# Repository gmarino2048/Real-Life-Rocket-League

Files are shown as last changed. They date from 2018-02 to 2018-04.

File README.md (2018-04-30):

# SocCar: Arcade Style Car-Soccer Game

## Getting Started:

### Basic Instructions

1. Locate a set of Cars, Arena, and ball near you.

2. Make sure both Cars, and the Arena are powered on. The power switch is located on the bottom of each car. If the arena appears to be without power, ensure that it is plugged in.

3. Go to SocCar website

4. Click on Play Game

5. Create a New User

6. Sign in with User Information

7. Make sure that your car is on

8. Press Play Game

## Troubleshooting:

### Connectivity:
If a car appears to be having an issue receiving commands:
1. Check the LED located on the Arduino Board on each Car. If the LED is lit, the car is properly powered.
2. If the car was not properly powered, try to turn the car off and on again. If the car still appears to be without power, contact your nearest SocCar vendor.
3. If the cars are properly powered, turn them off and on using the power switch located on the bottom of the car. This will reset the connection.

### Driving Issues:

#### If the speed of a car seems to be inconsistent:
1. Check the Drive Gears on either side of the car. Make sure that both gears are standing straight. If they are not straight, apply light pressure until you have righted them. Restart the car and try it again.
2. If the drive gears are straight, check to see if the steering assembly is flexing so the front two wheels are angled. If this is the case, your steering assembly likely

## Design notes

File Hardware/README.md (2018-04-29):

# SocCar Project

## Hardware

There are two important components of the hardware for this project: the arena and the car. The arena will display the players' usernames and scores, and will relay that information back to the server. The car will listen for input from the server, and will move accordingly so that the player is able to control the car to get the ball into the goal.

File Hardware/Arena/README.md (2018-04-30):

# SocCar Project

## Arena

### API Connection

The API Connection folder contains all of the source code for the connection between the backend and the Arena. If you're interested, there are some functional unit tests in there under the [src](https://github.com/gmarino2048/Real-Life-Rocket-League/tree/master/Hardware/Arena/API%20Connection/API%20Connection/src) folder.

If you are unsure of the login credentials for the project, please see the `ID and Secret.txt` file included.

### Arena Hardware

#### Microcontroller Programming

To program each of the microcontrollers, navigate to the Arduino folder. There should be three microcontrollers total: an Arduino Due, a Particle Photon, and an Arduino nano. The following list gives the steps to program each microcontroller successfully.

- Arduino Due -- has the most pins, ARM Processor, is the largest device of the three
  - Using the arduino application, load the Arena-Controller.ino sketch onto this device
  - Reset the Controller

- Particle Photon -- has the least pins, is the smallest device, has a blinking RGB LED
  - Go to build.particle.io
  - Log in and register the device to your account (follow the prompted steps)
  - Copy and paste the Web-Connection.ino file into the code window
  - Click "Flash", and wait for the device to update

- Arduino Nano -- small, but has more pins than the Photon, has  green and yellow LEDs which blink occasionally
  - Using the arduino application, load the LCD-Controller.ino sketch onto the device.
  - Occasionally, the bootloader of the device will be erased to fit the entire volume of the sketch into memory. If this occurs and you cannot load the code, see [this example.](https://www.arduino.cc/en/Tutorial/ArduinoISP)
  - Once the code has been uploaded, see the guide below for connecting each of the components.

#### Microcontroller Connection

Using the above information, connect each individual component according to the diagram found below:

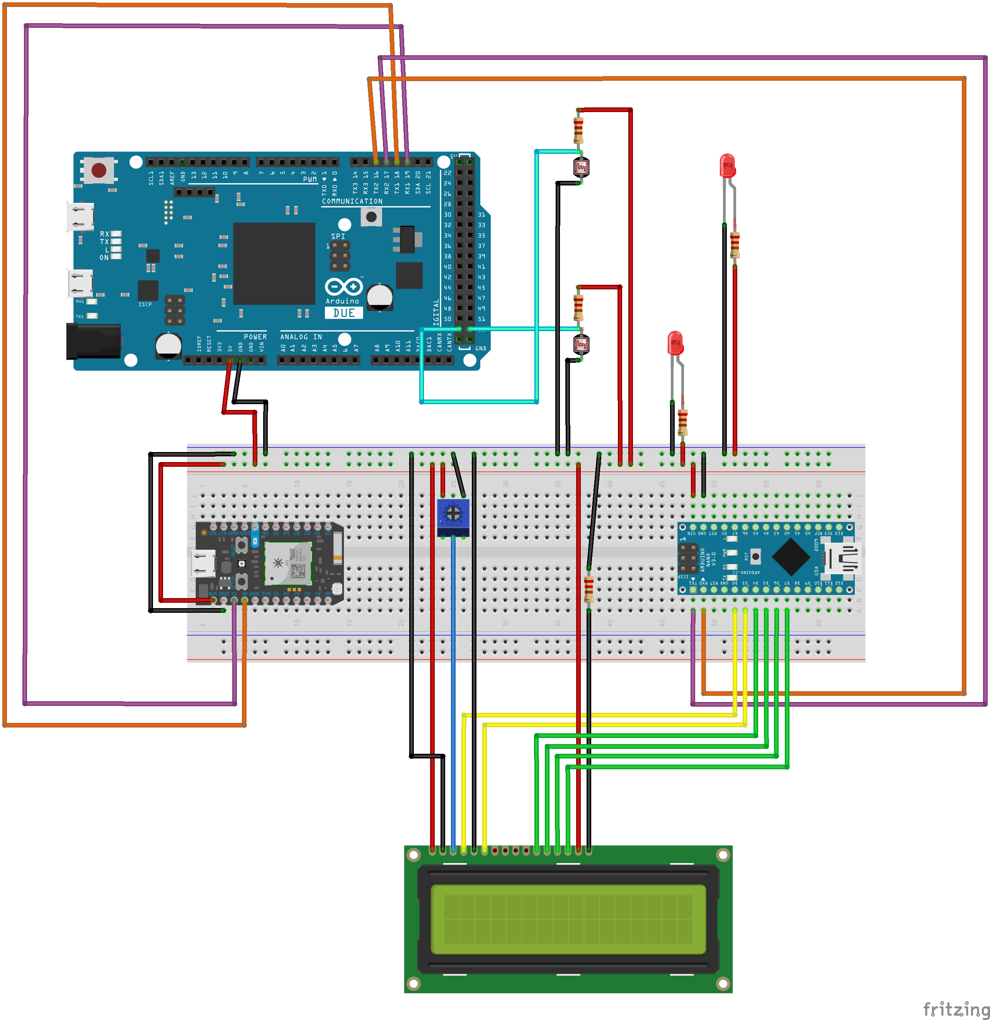
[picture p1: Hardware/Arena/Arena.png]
Arena Wiring Diagram


Note that the LCD Display is connected to the Arduino Nano, and the break beam sensors (modeled by a resistor and photoresistor in this case) are connected to the DUE.

Ensure that ALL of the connections are correct before supplying power to the devices, as incorrect connections could potentially damage certain components.

If you have any problems connecting the components, feel free to [open an issue](https://github.com/gmarino2048/Real-Life-Rocket-League/issues) on our github repository or [send one of us an email](gxm262@case.edu) for more help with the problem.

We hope you enjoy playing the game as much as we've enjoyed creating it :)

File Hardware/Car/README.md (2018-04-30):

## Car

#### car
all code in the car
#### everything else
solid works designs for the steering assembly

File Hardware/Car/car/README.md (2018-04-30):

##   Car code --> all code in each car.

####   carStateMachine: script running on arduino
####   /email_IP/sendIP.sh: shell script runs on start up
        ---> sends IP address of car to specified email
		---> calls processIP.py, and smtpCommands.sh to help
####   run: c script that runs after shell script
        ---> udp_run.c compiles to run, this is done prior to startup.
		---> calls serialComm.py, a script that goes between Pi and Arduino.
####   makefile: compiles udp_run.c

#####  remoteControlMod:
        ---> a lil bit of code I wrote for fun, that isn't really part of the project 
        ---> - but I didn't know where else to put it. 
        ---> if you have a linux machine it allows you to control the car without backend/frontend

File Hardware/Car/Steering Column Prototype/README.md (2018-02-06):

# Steering Column Prototype
## I'll get to this part later.

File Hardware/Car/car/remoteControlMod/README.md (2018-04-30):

##   Mod to control the car without backend/frontend

####	 run the modified version of udp_run_.c on the pi.
####   change ip in carCommander.sh to pi's current IP address.
####   run carCommander.sh on your linux machine, and follow instructions.

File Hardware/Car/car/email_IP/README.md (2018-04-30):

##  Code for Pi to send Current IP on start-up

Fixed the issue we were having with the car getting different IP addresses. Took Savi's idea, and implented it with two shell scripts and a python script. Store all commands in .txt files (in /commands/) so that the smtp request is easily changed by editing sendIP.sh.
I've configured the Pi to connect to the internet before it starts up. It then runs sendIP.sh at the end of its bootscript.

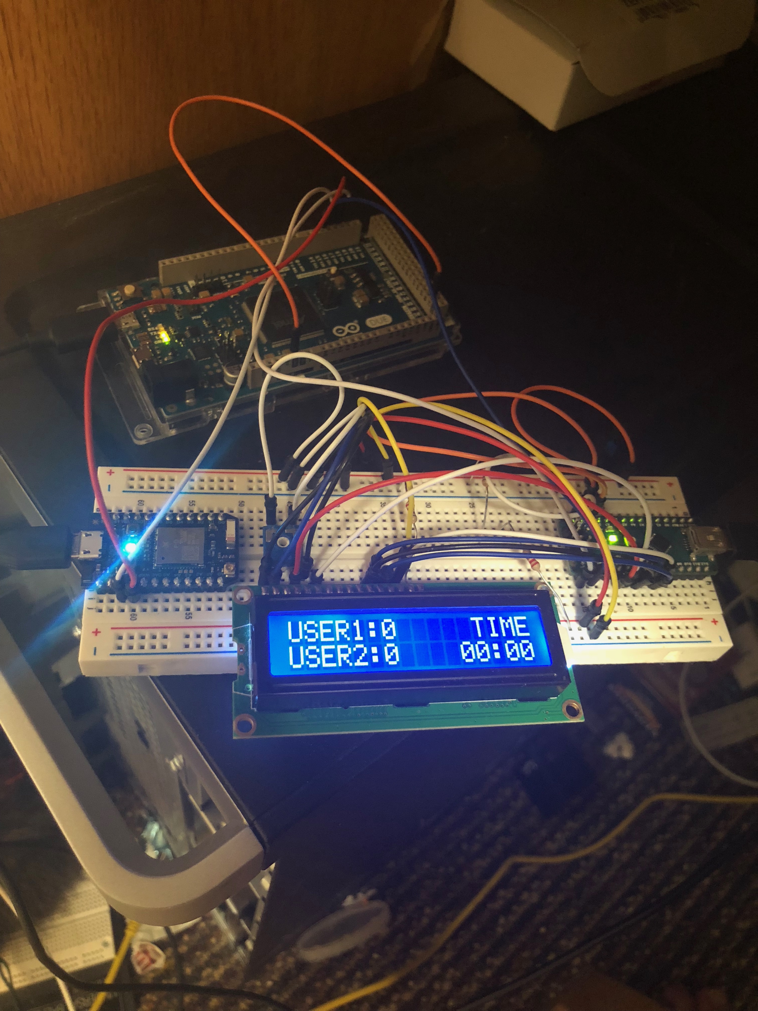
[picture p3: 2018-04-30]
Hardware/Arena/Arduino/Tests/SPEC - 10/Arena Function 1.jpg

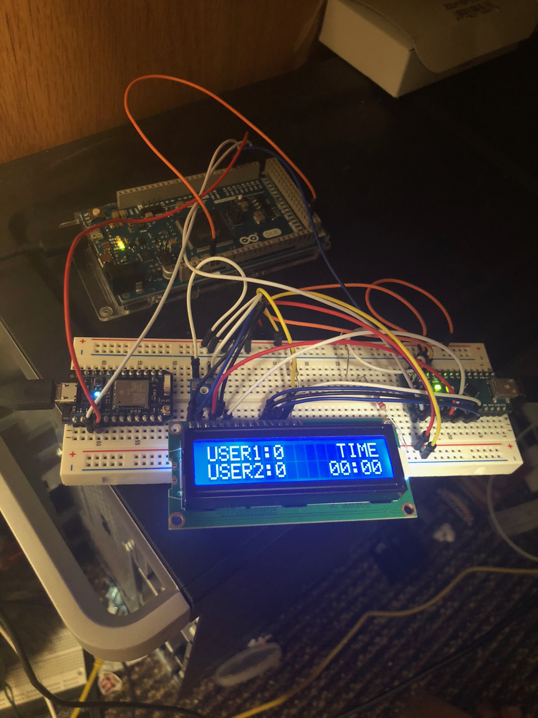
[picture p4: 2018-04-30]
Hardware/Arena/Arduino/Tests/SPEC - 10/Arena Function 2.jpg

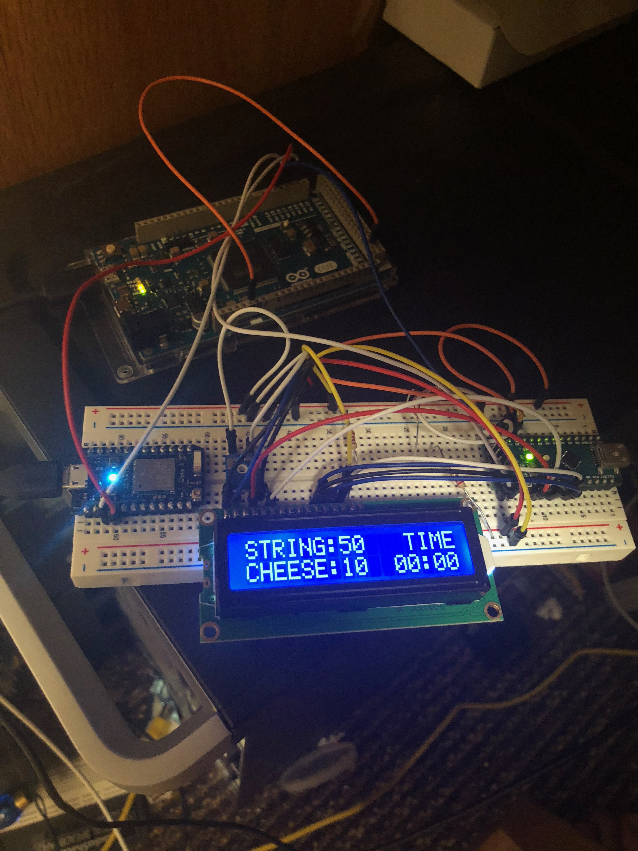
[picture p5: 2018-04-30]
Hardware/Arena/Arduino/Tests/SPEC - 10/Arena Function 4.jpg

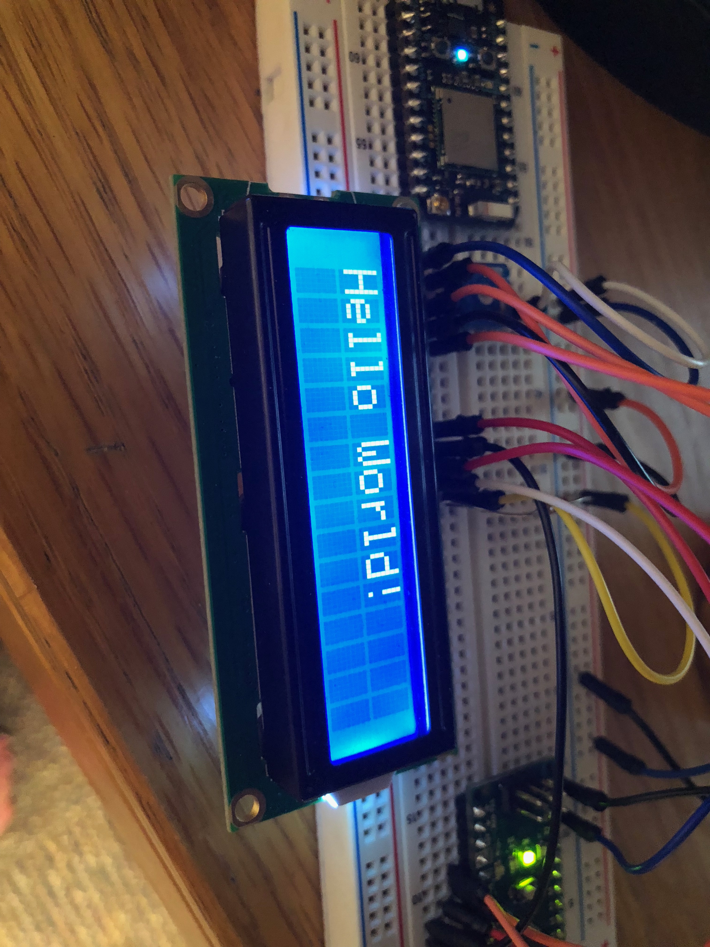
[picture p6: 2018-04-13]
Hardware/Arena/Arduino/Tests/SPEC - 00/Side View 1.jpg

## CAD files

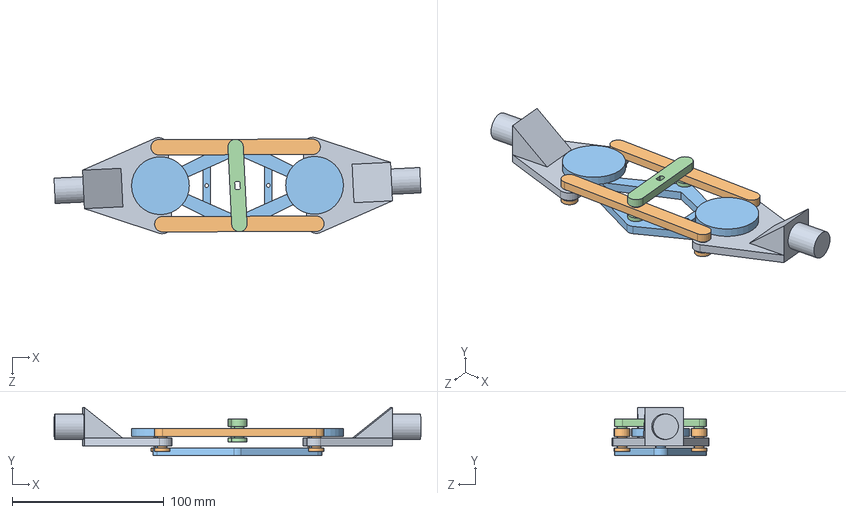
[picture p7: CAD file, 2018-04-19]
Hardware/Car/Steering Column/Steering Column Assembly.SLDASM
241.9 x 31.8 x 63.7 mm
Axel Rotator x 2
Stabilization Bar x 2
Steering Column Base New
Driver Bar

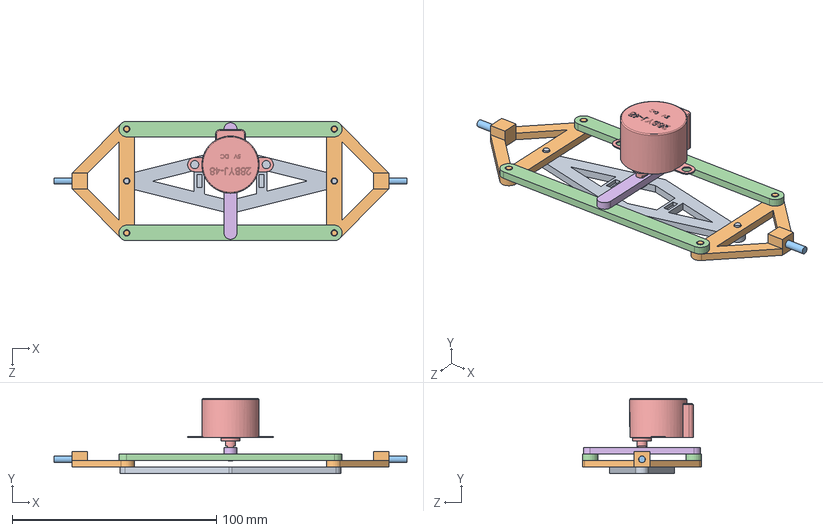
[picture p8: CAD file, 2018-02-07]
Hardware/Car/Steering Column Prototype/Solidworks Parts/Steering Column Assembly.SLDASM
172.7 x 36.8 x 58.4 mm
Mount Base
Axle Control x 2
Axle x 2
Connection Bar x 2
Stepper 28BYJ48
Driver Bar

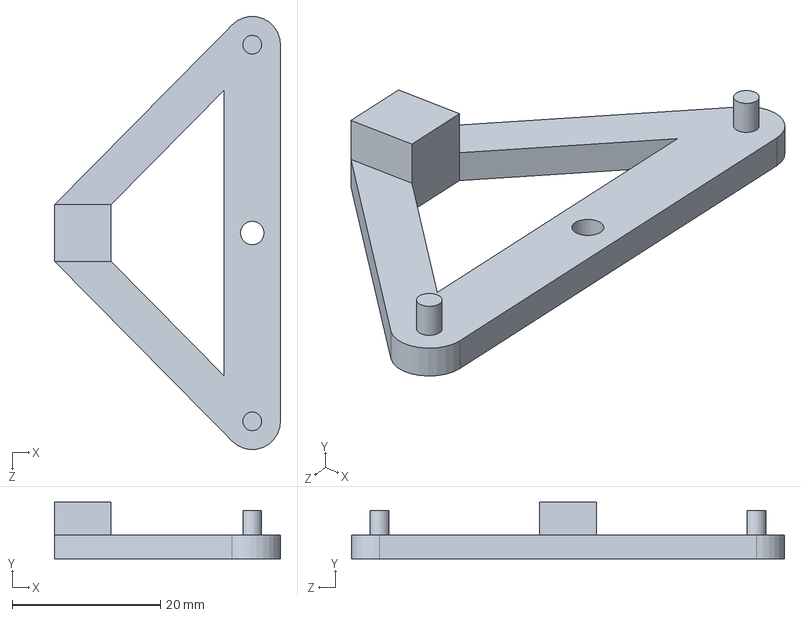
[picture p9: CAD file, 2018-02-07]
Hardware/Car/Steering Column Prototype/Solidworks Parts/Axle Control.SLDPRT
30.5 x 7.62 x 58.4 mm

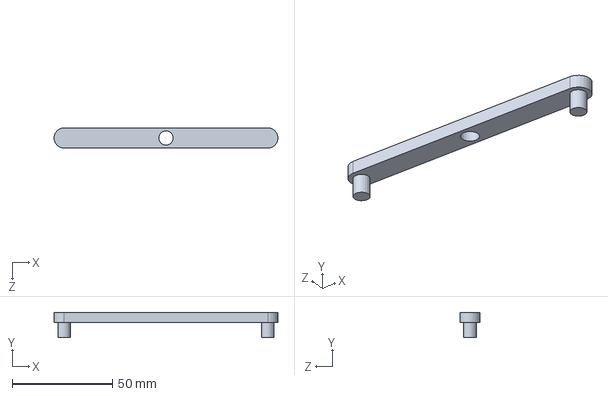
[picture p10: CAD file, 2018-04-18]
Hardware/Car/Steering Column/No Caps/Stabilization Bar No Caps.SLDPRT
111.8 x 12.7 x 10.2 mm

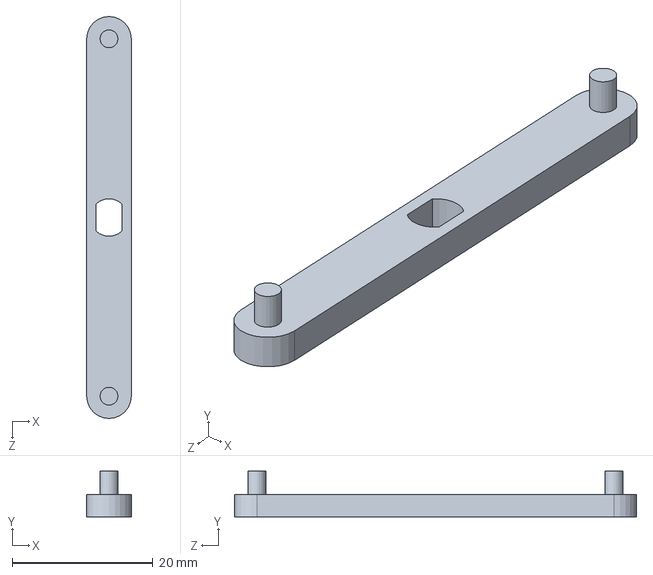
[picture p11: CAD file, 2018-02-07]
Hardware/Car/Steering Column Prototype/Solidworks Parts/Driver Bar.SLDPRT
6.35 x 6.48 x 57.1 mm

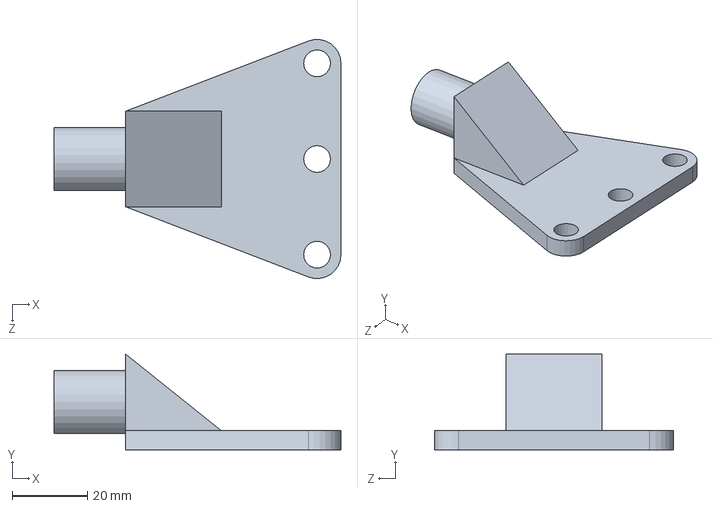
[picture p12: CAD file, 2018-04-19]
Hardware/Car/Steering Column/Axel Rotator.SLDPRT
76.2 x 25.4 x 63.4 mm

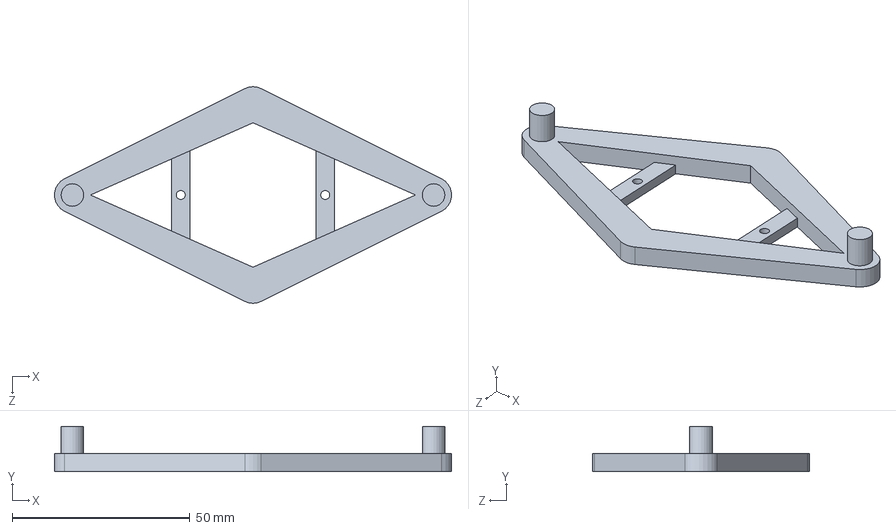
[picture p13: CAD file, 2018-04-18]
Hardware/Car/Steering Column/No Caps/Steering Column Base No Caps.SLDPRT
111.7 x 12.7 x 61.0 mm

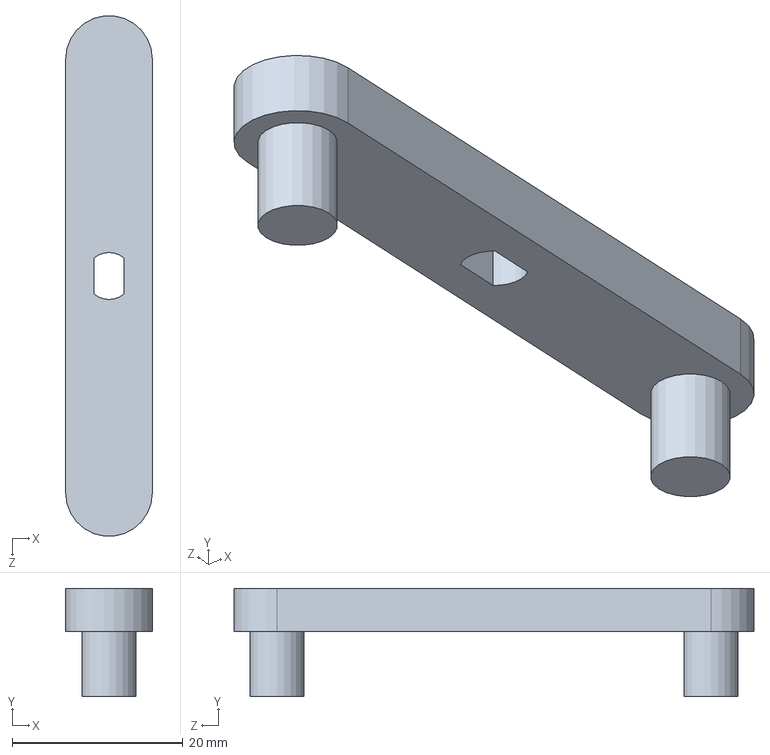
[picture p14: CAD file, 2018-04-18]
Hardware/Car/Steering Column/No Caps/Driver Bar No Caps.SLDPRT
10.2 x 12.7 x 60.9 mm

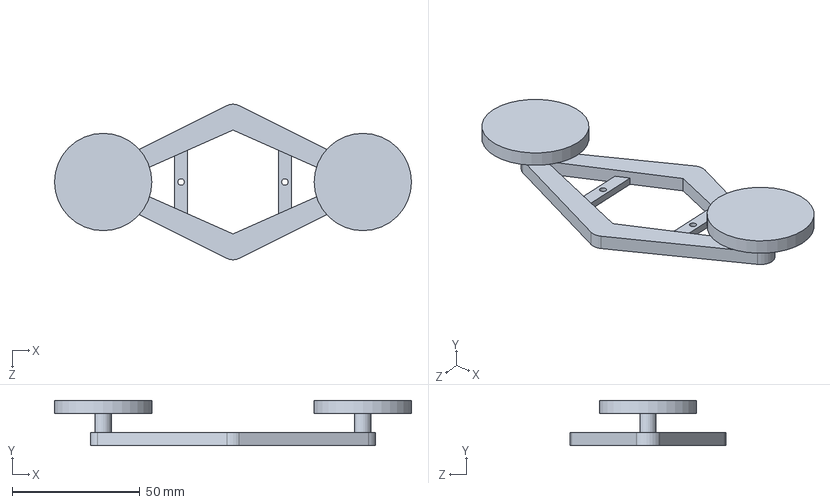
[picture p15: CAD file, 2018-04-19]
Hardware/Car/Steering Column/Steering Column Base New.SLDPRT
139.7 x 17.8 x 61.0 mm

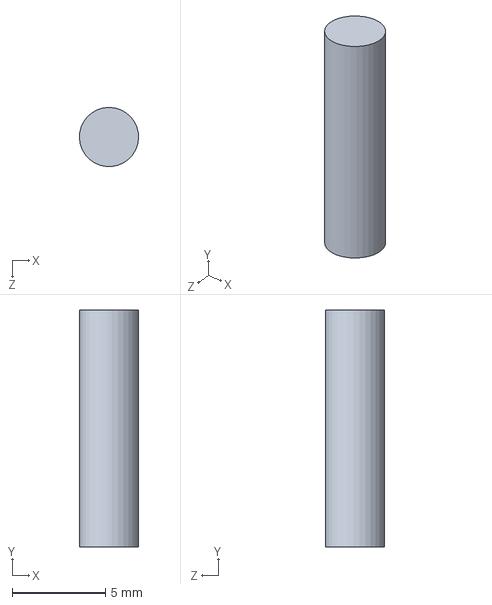
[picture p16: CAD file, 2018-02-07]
Hardware/Car/Steering Column Prototype/Solidworks Parts/Axle.SLDPRT
3.17 x 12.7 x 3.17 mm

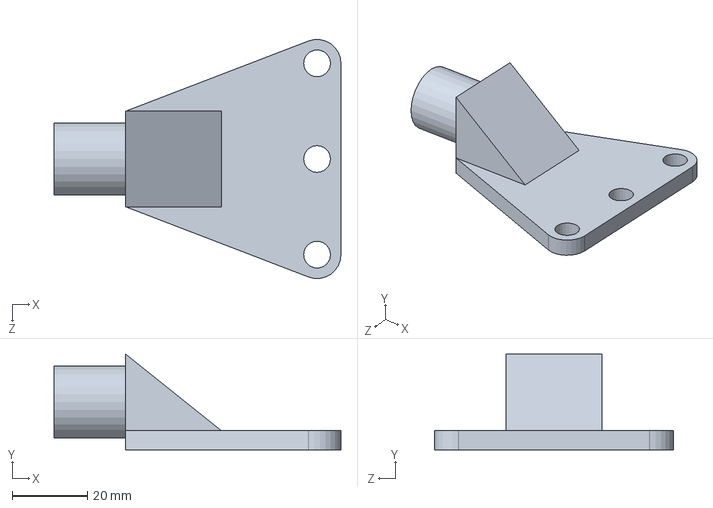
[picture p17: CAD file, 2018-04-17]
Hardware/Car/Steering Column/No Caps/Axel Rotator.SLDPRT
76.2 x 25.4 x 63.4 mm

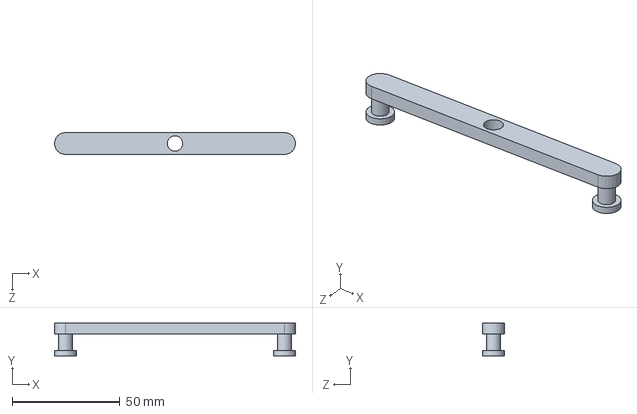
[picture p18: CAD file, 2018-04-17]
Hardware/Car/Steering Column/Stabilization Bar.SLDPRT
111.8 x 15.2 x 10.2 mm

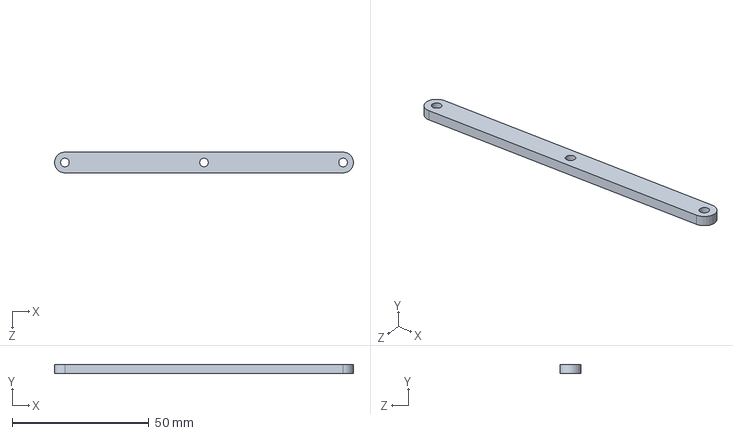
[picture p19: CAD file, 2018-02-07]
Hardware/Car/Steering Column Prototype/Solidworks Parts/Connection Bar.SLDPRT
109.2 x 3.17 x 7.62 mm

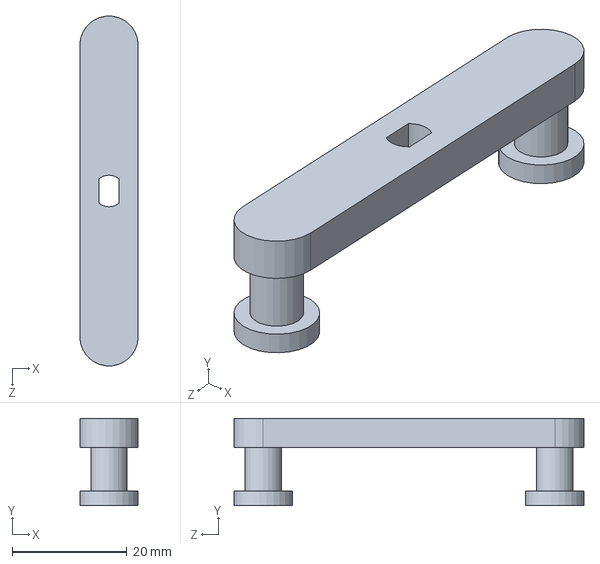
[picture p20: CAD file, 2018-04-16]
Hardware/Car/Steering Column/Driver Bar.SLDPRT
10.2 x 15.2 x 61.0 mm

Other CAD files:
Hardware/Car/Steering Column Prototype/Solidworks Parts/Mount Base.SLDPRT
Hardware/Car/Steering Column/Steering Column Base.SLDPRT
Hardware/Car/Steering Column Prototype/Solidworks Parts/Stepper 28BYJ48.SLDPRT
Hardware/Car/Steering Column Prototype/Solidworks Parts/STL/Axle.STL
Hardware/Car/Steering Column Prototype/Solidworks Parts/STL/AxleControl.STL
Hardware/Car/Steering Column Prototype/Solidworks Parts/STL/ConnectionBar.STL
Hardware/Car/Steering Column Prototype/Solidworks Parts/STL/DriverBar.STL
Hardware/Car/Steering Column Prototype/Solidworks Parts/STL/MountBase.STL

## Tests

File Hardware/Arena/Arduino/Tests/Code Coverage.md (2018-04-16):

# Code Coverage Estimate

## Arduino Code Test Coverage: 87%

The method by which this coverage was estimated was by taking the individual functions that were going to be tested and counting the number of lines in each file to be ported to the test files. The total number of lines in the functions to be tested were then divided by the total number of functional lines in the entire project.

The functional tests of the Arduino Code are currently incomplete, and there is no code coverage software to aid in the testing process, so I have had to do all of the code coverage estimations by hand. Given this, I expect the code coverage estimate to be accurate in this case. The actual coverage should be within 5% of the actual value.

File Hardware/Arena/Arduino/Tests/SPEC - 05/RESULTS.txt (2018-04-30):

TEST RESULT: PASS

The Arduino due was able to successfully print out the
strings given to the particle photon on the site
console.particle.io showing that the interfacing between
the photon and the due was a complete success.

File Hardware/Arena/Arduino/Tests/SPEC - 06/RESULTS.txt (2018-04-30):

TEST RESULT: PASS

The Photon was easily able to output all of the text given
to it by the Arduino due. This demonstrates that the connection
between them is solid.

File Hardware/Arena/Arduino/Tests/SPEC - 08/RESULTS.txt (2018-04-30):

TEST RESULT: PASS

The arena can send data back and forth across all three
devices without issue.

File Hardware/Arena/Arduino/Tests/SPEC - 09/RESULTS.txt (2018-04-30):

TEST RESULT: PASS

The Arduino due is completely capable of breaking down
each message into its component parts and parsing them for
the important bits of each message.

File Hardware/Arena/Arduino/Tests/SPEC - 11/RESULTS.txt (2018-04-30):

TEST RESULT: DEPRICATED

This test has been depricated due to the fact that error
checking is built in to Arduino serial communication, and
we do not have to do it manually.

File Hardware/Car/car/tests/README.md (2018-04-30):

## Code Modules:
    UDP Server (Module 1)
    Serial Connection (Module 2)
    State Machine (Module 3)
    UDP Server --> Serial Connection --> State Machine (Module 4)

##  Tests:
    udp_test suite --> Tests Module 1
                 --> for speed
                 --> for reliability
    isolated_serial suite --> Tests Module 2
                 --> for reliability
    hardware suite --> Tests Module 3
                 --> checks if Hardware works (Module 3)
    timed_stepper suite --> Tests Module 3
                 --> checks functionality of Module 3
    serial_test suite --> Tests Module 4
                 --> checks reliability of connections
    clutter suite --> Tests Module 4
                 --> checks responsiveness of machine accross
                     connections with increasing command frequency

##  Coverage:
    As my tests are functional, I can only show that each of my tests
    covers a specific "module" of code. Tests covering Module 4 test
    that not only does each module test sufficiently, but that they
    test in concert together.
    My tests also target various performance barriers (namely time),
    and test the limitations set by the environment (the environment
    here is the UDP connection being used, which has the limitation of
    being lossy).
    While 100% of the code is tested, the data used to test the code
    is completely based on the possible values that could exist in
    framework the car was designed to work in. Thus this code is
    untested for use outside of the designed system for our project,
    which means that it relies heavily on the the accuracy (and
    therefore testing) of the other project components.

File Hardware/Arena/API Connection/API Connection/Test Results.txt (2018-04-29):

TEST RESULTS

The API Connection Test hits approximately 85 - 90% of our source code.
However, this depends heavily on the manual user input, so below I will
cover how to achieve maximal code coverage on a single run:

1. Start the APIConnectionTest Class

2. Enter the correct information. See ID and Secret.txt

3. Be sure to answer "no" when prompted at least once for each field

4. When prompted for the cipher key, be sure to remember which one you 
used!!! Default value is "Password"

5. Wait one minute

6. When prompted for a new cipher key, enter a bad one at least once
before entering the correct value. This should be the same one used
in step 4

7. View results!

The above method should give 60% code coverage overall, with 85% coverage
on the authenticator, 70% coverage on the OAuthFileManager, and 88% coverage
on the APIConnection.

It was deemed too inefficient to attempt to generate another test case for the
Authenticator, as the few methods which could be tested involved encryption and
decryption, each of which are fully covered by using the example above. Besides,
if anything goes wrong in the encryption and decryption process

Since the OAuth File manager did not have excellent coverage using the 
APIConnectionTest class, a second test suite was designed to be run against
the OAuthFileManager. These tests get a coverage of about 93% on the 
OAuthFileManager.

All tests report PASS.

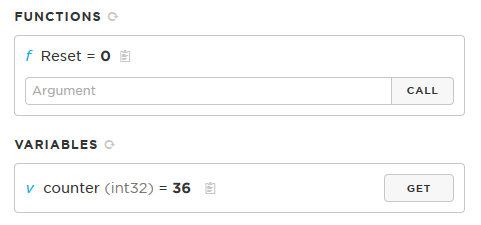
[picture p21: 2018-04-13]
Hardware/Arena/Arduino/Tests/SPEC - 03/Function and Variable Result.PNG

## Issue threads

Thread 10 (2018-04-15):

Arduino Timing

gjbsaiia, 2018-04-15:
Having issues using timed loops in Arduino - can't seem to use millis() correctly in order to time actions. This is a major concern as this is a vital piece of functionality to execute boost properly.

gjbsaiia, 2018-04-15:
Experimenting with this using the stepper motor - I seem to have a better understanding for how millis() functions in arduino

gjbsaiia, 2018-04-15:
I have implemented timing properly in the state machine - every thing seems to be working correctly. Will do further testing

gjbsaiia, 2018-04-15:
We good homie

Closed 2018-04-15.

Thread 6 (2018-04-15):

Formatting Error with Boost/Game board

BrieLemon, 2018-04-15:
//Car Code
var rCar;
var bCar;
var myBackground;
function startGame() {
    /*bCar = new component(40, 40, "new-blue-car-cartoon-transportation-free-sports.png", 300, 120, "image");*/
    rCar = new component(40, 40, "red_car.png", 540, 120, "image");
    myBackground = new component(880, 470, "soccer_field_311115.jpg", 0, 0, "image");
    arena.start();
}
var arena = {
    canvas: document.createElement("canvas"), start: function () {
        this.canvas.width = 880;
        this.canvas.height = 470;
        this.context = this.canvas.getContext("2d");

        document.body.insertBefore(this.canvas, document.body.childNodes[0]);
        this.interval = setInterval(updateArena, 20);

        window.addEventListener('keydown', function (e) {
            arena.key = e.keyCode;
        })
        window.addEventListener('keyup', function (e) {
            arena.key = false;
        })
    },
    clear: function () {
        this.context.clearRect(0, 0, this.canvas.width, this.canvas.height);
    }
}
function component(width, height, color, x, y, type) {
    this.type = type;
    if (type == "image") {
        this.image = new Image();
        this.image.src = color;
    }
    this.area = arena
    this.width = width;
    this.height = height;
    this.speedX = 0;
    this.speedY = 0;
    this.x = x;
    this.y = y;
    this.update = function () {
        ctx = arena.context;
        if (type == "image") {
            ctx.drawImage(this.image, this.x, this.y, this.width, this.height);
        } else {
            ctx.fillStyle = color;
            ctx.fillRect(this.x, this.y, this.width, this.height);
        }
    }
    this.newPos = function () {
        this.x += this.speedX;
        this.y += this.speedY;
    }
}
/*Key Pressed*/
function updateArena() {
    arena.clear();
    myBackground.newPos();
    myBackground.update();
    rCar.newPos();
    rCar.update();
    rCar.speedX = 0;
    rCar.speedY = 0;

    /*bCar.newPos();
    bCar.update();
    bCar.speedX = 0;
    bCar.speedY = 0;*/

    //left arrow
    if (arena.key && arena.key == 37) {
        rCar.speedX = -1;
    }
    //right arrow
    if (arena.key && arena.key == 39) {
        rCar.speedX = 1;
    }
    //up arrow
    if (arena.key && arena.key == 38) {
        rCar.speedY = -1;
    }
    //down arrow
    if (arena.key && arena.key == 40) {
        rCar.speedY = 1;
    }
    //left (a)
    if (arena.key && arena.key == 65) {
        rCar.speedX = -1;
    }
    //right (d)
    if (arena.key && arena.key == 68) {
        rCar.speedX = 1;
    }
    //up (w)
    if (arena.key && arena.key == 87) {
        rCar.speedY = -1;
    }
    //down (s)
    if (arena.key && arena.key == 83) {
        rCar.speedY = 1;
    }
    rCar.newPos();
    rCar.update();

    rCar.newPos();
    rCar.update();
}
document.getElementById("buttonQ").onclick = function () {
    location.href = "EndGame.html";
}
/*
//Boost Code
    var fill = true;
    var percentage = 0;
    var increase = 10;
    var max = 100;

function boost() {
 //Load Boost
    if (fill == true && <= max) {
        percentage += increment
        if (value == ceiling) {
            fill = false;
        }
//Using boost
    } else {
        fill = false;
        percentage -= increase;

        if (percentage == 0) {
            fill = true;
        }
    }
    document.getElementById('counter').innerHTML = percentage;
}
setInterval(boost, 1000);

//Time Code
var startTime = -1;
var animationLength = 2000; // Animation length in milliseconds

function doAnimation(timestamp) {
    // Calculate animation progress
    var progress = 0;

    if (startTime < 0) {
        startTime = timestamp;
    } else {
        progress = timestamp - startTime;
    }

    // Do animation ...
    if (progress < animationLength) {
        window.requestAnimationFrame(doAnimation);
    }
}

// Start animation
window.requestAnimationFrame(doAnimation);

function redraw() {
    drawPending = false;
    // Do drawing ...
}

var drawPending = false;
function requestRedraw() {
    if (!drawPending) {
        drawPending = true;
        window.requestAnimationFrame(redraw);
    }
}
animator.requestAnimationFrame =
    function (callback) {
        window.requestAnimationFrame(function (t) {
            callback(t);
            redraw();
        });
    };*/

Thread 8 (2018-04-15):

IP Address changing

gjbsaiia, 2018-04-15:
On case wifi addresses are allocated by router regardless of whether you are continuously connected or you reconnect at a different location. This creates an issue for communication across components, as we necessarily need each other's IPs to use socket communication.

gjbsaiia, 2018-04-30:
Savi had the idea to write a shell script that runs at the the boot up of the pi. I wrote it in two .sh scripts and a python script, it's in "../car/email_IP/ ".

Closed 2018-04-30.

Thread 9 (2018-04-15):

Steering Column to Wheel ratio

gjbsaiia, 2018-04-15:
The steering column is way too shrimpy in proportion to the wheels that were purchased - there is no way they will support the wait. I've tried scaling it - it's just too shrimpy.

gjbsaiia, 2018-04-15:
Guy is redesigning the steering column based on the new dimensions

Closed 2018-04-15.

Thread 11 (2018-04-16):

Error connecting to SQL database

nkchakra, 2018-04-16:
`private static final String DB_URL = "jdbc:mysql://127.0.0.1:3306/SocCar?autoReconnect=true&useSSL=false";
	private static final String username = "root";
	private static final String password = "SocCar";
	private static final String userTable = "Users";
	private static final String gameTable = "Games";

	private static final String salt = "lkj13487fd0hj24";

	private Connection connection;
	private Statement statement;
	private ResultSet result;

	public ResultSet getResult() {
		return result;
	}

	public MySQL_Connector() {

		try {
			this.connection = DriverManager.getConnection(DB_URL, username, password);
			this.statement = this.connection.createStatement();
		} catch (SQLException e) {
			// TODO Auto-generated catch block
			System.out.println("SQL connection failed");
			e.printStackTrace();
		}

	}`

Had to add the 'autoConnect' and 'useSSL' tags to the url of the database

Closed 2018-04-16.

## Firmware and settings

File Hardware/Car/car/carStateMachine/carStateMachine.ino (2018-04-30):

//Griffin Saiia, Gjs64
//SocCar: Car State Machine

/*
STATE TABLE
'a' - start/end game, handled inside serialEvent()
'0' - neutral
'1' - Forward, drive()
'2' - Turn Right, right()
'3' - Reverse, reverse()
'4' - Turn Left, left()
'5' - Forward+Right, rdrive()
'6' - Forward+Left, ldrive()
'7' - Reverse+Right, rreverse()
'8' - Reverse+Left, lreverse()
'9' - Brake, brake()
'b' - boost, boost()
*/


//*******************Global Variables and Definitions*******************

  //*************turn motor (stepper motor)*****************
  #define enS   3//pin
  #define sIn1  4//pin
  #define sIn2  5//pin
  #define sIn3  6//pin
  #define sIn4  7//pin
  //delay between polarity shifts for stepper
  #define DELAYTIME  1//ms
  //how long steppers should run for 90 degree turn
  #define TURNTIME  400//ms

  //******************drive motor***************************
  //enable allows for in1/in2 to accept input and takes rpm
  #define enA  8//pin
  #define enB 11//pin
  //foward
  #define rin1  9//pin
  #define lin1 12//pin
  //reverse
  #define rin2  10//pin
  #define lin2 13//pin
  //normal speed
  #define NSPD  150//rpm

  //********************boost state*************************
  //boost speed
  #define BSPD  250//rpm
  //boost duration
  #define BDUR  3000//ms
  //cooldown duration
  #define CDUR  9000//ms
  //flag to indicate if boost is active
  int boostSet;
  //flag to indicate if boost CAN be active
  int bReady;
  //how long boost has been active, global as all states must check this
  unsigned long bTimer;
  //how long since last boosted
  unsigned long cooldown;

  //**********************program state*********************
  //timer for whole program
  unsigned long totalTime;
  //current state of program
  char state;
  //needed to check against state in case of new game
  char newState;
  //current wheel position: 0 straight, 1 right, -1 left
  int lastTurn;
  //rpm enA is set to, changes depending on boost
  int driveSpeed;

//****************************Utility Functions***************************

void setup(){
  //sets drive motor control pins to output
  pinMode(enA, OUTPUT);
  pinMode(rin1, OUTPUT);
  pinMode(rin2, OUTPUT);
  pinMode(enB, OUTPUT);
  pinMode(lin1, OUTPUT);
  pinMode(lin2, OUTPUT);
  //sets stepper control pins
  pinmode(enS, OUTPUT);
  pinMode(sIn1, OUTPUT);
  pinMode(sIn2, OUTPUT);
  pinMode(sIn3, OUTPUT);
  pinMode(sIn4, OUTPUT);
  //sets default game state values
  driveSpeed = NSPD;
  state = 'a';
  lastTurn = 0;
  bReady = 1;
  boostSet = -1;
  totalTime = millis();
  Serial.begin(9600);//sets baud rate
}

//called at end of loop whenever there is new serial data
void serialEvent(){
  while(Serial.available()){
    state = (char)(Serial.read());
  }
  if(state == 'a'){
    straight();
    brake();
    setup();
  }
  if(state == '9'){
    state = '0';
    brake();
  }
}

//stepper helper funtion - just sets all stepper pins low
void stepOff(){
  digitalWrite(enS, LOW);
  digitalWrite(sIn1, LOW);
  digitalWrite(sIn2, LOW);
  digitalWrite(sIn3, LOW);
  digitalWrite(sIn4, LOW);
}

//right 1, left -1
void stepRoutine(int lOrR, unsigned long time){
  //so that they can be set in loop
  stepOff();
  digitalWrite(enS, HIGH);
  int stepPins[] = {sIn1, sIn2, sIn3, sIn4};
  int i;
  if(lOrR){
    //start rotating clockwise
    i = 0;
  }
  else{
    //start rotation counter clockwise
    i = 3;
  }
  //to time our loop
  totalTime = millis();
  unsigned long loopTime = millis();
   while((loopTime - totalTime) < time){
    if(((i-lOrR)%4) < 0){
      digitalWrite(stepPins[3], LOW);
    }
    else{
      digitalWrite(stepPins[(i-lOrR)%4], LOW);
    }
    digitalWrite(stepPins[i%4], HIGH);
    delay(DELAYTIME);
    //using lOrR here because for left (counter clockwise), i needs to decrease
    //                        for right (clockwise), i needs to increase
    if(((i+lOrR)%4) < 0){
      digitalWrite(stepPins[3], HIGH);
      i = 3;
    }
    else{
      digitalWrite(stepPins[(i+lOrR)%4], HIGH);
      i = i + lOrR;
    }
    delay(DELAYTIME);
    loopTime = millis();
  }
  //stepper off
  stepOff();
}

//makes sure wheels are straight
void straight(){
  if(lastTurn != 0){
    stepRoutine((lastTurn * -1), TURNTIME);
    lastTurn = 0;
  }
}

//method to keep boost in real time
void checkBoost(){
  totalTime = millis();
  if(boostSet){
    if((totalTime - bTimer) > BDUR){
      toggleBoost();
    }
  }
  else if(!bReady){
    if((totalTime - cooldown) > CDUR){
      bReady = 1;
    }
  }
}

//only called at the end of a boost period, or at the start of one
//important to handle boost timers
void toggleBoost(){
  boostSet = !boostSet;
  if(boostSet){
    driveSpeed = BSPD;
    bTimer = millis();
    bReady = -1;
  }
  else{
    driveSpeed = NSPD;
    cooldown = millis();
  }
}

//****************************State Functions*****************************

//drive, we're going forward now
//takes direction
//states '1', '5', and '6'
void drive(int turn){
  if(turn == 0){
    //sets wheels straight
    straight();
  }
  else{
    if(turn){
      right();
    }
    else{
      left();
    }
  }
  analogWrite(enA, driveSpeed);
  analogWrite(enB, driveSpeed);
  digitalWrite(lin1, HIGH);
  digitalWrite(lin2, LOW);
  digitalWrite(rin1, LOW);
  digitalWrite(rin2, HIGH);
}

//reverse, we're going backwards
//takes direction
//states '3', '7', '8'
void reverse(int turn){
  if(turn == 0){
    //sets wheels straight
    straight();
  }
  else{
    if(turn){
      right();
    }
    else{
      left();
    }
  }
  analogWrite(enA, driveSpeed);
  analogWrite(enB, driveSpeed);
  digitalWrite(lin1, LOW);
  digitalWrite(lin2, HIGH);
  digitalWrite(rin1, HIGH);
  digitalWrite(rin2, LOW);
}

//right, turning right, '2'
void right(){
  //if we're left, we have to turn twice as far to be right
  if(lastTurn == -1){
    stepRoutine(1, (TURNTIME * 2));
  }
  //base case, we're straight
  else if(lastTurn == 0){
    stepRoutine(1, TURNTIME);
  }
  //if we're right, do nothing
  lastTurn = 1;
}

//left, we're turning left, '4'
void left(){
  //will only be true if we're turned right
  if(lastTurn){
    stepRoutine(-1, (TURNTIME * 2));
  }
  //base case, we're straight
  else if(lastTurn == 0){
    stepRoutine(-1, TURNTIME);
  }
  //if already left do nothing
  lastTurn = -1;
}

void brake(){
  digitalWrite(enA, LOW);
  digitalWrite(lin1, LOW);
  digitalWrite(lin2, LOW);
  digitalWrite(enB, LOW);
  digitalWrite(rin1, LOW);
  digitalWrite(rin2, LOW);
  digitalWrite(sIn1, LOW);
  digitalWrite(sIn2, LOW);
  digitalWrite(sIn3, LOW);
  digitalWrite(sIn4, LOW);
}

//boost, things are about to get faster 'b'
void boost(){
  //checks if we are allowed to boost
  if(bReady){
    toggleBoost();
  }
  analogWrite(enA, driveSpeed);
}

//*******************************Control Loop******************************

void loop(){
  //called at beginning of each iteration, includes totalTime update
  checkBoost();
  //this is first just because it should have fastest response
  if(state == '9'){
    state = '0';
    brake();
  }
  if(state == '1'){
    state = '0';
    drive(0);
  }
  if(state == '2'){
    state = '0';
    right();
  }
  if(state == '3'){
    state = '0';
    reverse(0);
  }
  if(state == '4'){
    state = '0';
    left();
  }
  if(state == '5'){
    state = '0';
    drive(1);
  }
  if(state == '6'){
    state = '0';
    drive(-1);
  }
  if(state == '7'){
    state = '0';
    reverse(1);
  }
  if(state == '8'){
    state = '0';
    reverse(-1);
  }
  if(state == 'b'){
    state = '0';
    boost();
  }
}

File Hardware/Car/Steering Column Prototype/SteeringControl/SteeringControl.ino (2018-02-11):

//Guy Marino
//gxm262

//Simple steering control to run the motor which powers the
//steering column
/*
#include<AccelStepper.h>

#define INPUT_1 3
#define INPUT_2 4
#define INPUT_3 5
#define INPUT_4 6

#define HALFSTEP 8

AccelStepper stepper1(HALFSTEP, INPUT_1, INPUT_2, INPUT_3, INPUT_4);

void setup () {
  pinMode(13, OUTPUT);
  pinMode(INPUT_1, OUTPUT);
  pinMode(INPUT_2, OUTPUT);
  pinMode(INPUT_3, OUTPUT);
  pinMode(INPUT_4, OUTPUT);

  stepper1.setMaxSpeed(2000.0);
  stepper1.move(1);
  stepper1.setAcceleration(100.0);
  stepper1.setSpeed(1000);
  stepper1.moveTo(0);
  stepper1.run();
}

void loop () {
  digitalWrite(13, HIGH);
  stepper1.moveTo(2000);
  stepper1.run();
  delay(1000);
  digitalWrite(13, LOW);
  stepper1.moveTo(-2000);
  delay(1000);
}
*/

#include <AccelStepper.h>
#define HALFSTEP 8

// Motor pin definitions
#define motorPin1  3     // IN1 on the ULN2003 driver 1
#define motorPin2  4     // IN2 on the ULN2003 driver 1
#define motorPin3  5     // IN3 on the ULN2003 driver 1
#define motorPin4  6     // IN4 on the ULN2003 driver 1

// Initialize with pin sequence IN1-IN3-IN2-IN4 for using the AccelStepper with 28BYJ-48
AccelStepper stepper1(HALFSTEP, motorPin1, motorPin3, motorPin2, motorPin4);

void setup() {
  stepper1.setMaxSpeed(1000.0);
  stepper1.setAcceleration(100.0);
  stepper1.setSpeed(200);
  stepper1.moveTo(20000);

}//--(end setup )---

void loop() {

  //Change direction when the stepper reaches the target position
  if (stepper1.distanceToGo() == 0) {
    stepper1.moveTo(-stepper1.currentPosition());
  }
  stepper1.run();
}

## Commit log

2018-02-06 New solidworks parts
    [Mount Base.SLDPRT, Steering Column Assembly.SLDASM, Stepper 28BYJ48.SLDPRT]
2018-02-07 New axle control part
    [Axle Control.SLDPRT, Mount Base.SLDPRT, Steering Column Assembly.SLDASM]
2018-02-07 Assembly Mostly Complete. Just missing Motor housing atm
    [Axle Control.SLDPRT, Axle.SLDPRT, Connection Bar.SLDPRT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]
2018-02-08 Some housekeeping and other slight changes
    [Axle Control.SLDPRT, Axle.SLDPRT, Connection Bar.SLDPRT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]
2018-02-08 STL Files for printing
    [Axle.STL, AxleControl.STL, ConnectionBar.STL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]
2018-02-11 New sld files
    [project.cfg]
2018-03-29 Moved Steering column prototype to the Car folder
    [Axle Control.SLDPRT, Axle.SLDPRT, Axle.STL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]
2018-03-29 New blank methods for Authenticator.java. Added more java classes and set the ground work for token encryption and storage
2018-03-31 setEncryptionKey updated to print out message to user
2018-04-03 Add to reconfigure my git setup... was super screwed up. This commit fixed the file structure, and has all the new tests I wrote. Also contains further updated car code.
    [carStateMachine.ino, serialComm.py, serial_test.ino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]
2018-04-13 Change
    I changed it to one folder as well as I switched to only have the red car.
2018-04-15 Fixed the Button
2018-04-15 New Steering Column Base
    [Steering Column Base.SLDPRT]
2018-04-16 New steering column base, Assembly created using the base and driver bars.
    [Stabilization Bar.SLDPRT, Steering Column Assembly.SLDASM, Steering Column Base New.SLDPRT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]
2018-04-16 Added new driver bar to the steering column
    [Driver Bar.SLDPRT]
2018-04-16 Driver bar added to the steering column assembly
    [Steering Column Assembly.SLDASM]
2018-04-16 Added driver hole to driver bar
    [Driver Bar.SLDPRT, Steering Column Base.SLDPRT]
2018-04-16 Code Coverage Estimate Created
    An estimate of the code coverage for the Arduino Code
2018-04-16 Attempting to merge
    [Steering Column Assembly.SLDASM]
2018-04-17 Loosened Tolerances on steering column assembly
    [Axel Rotator.SLDPRT, Stabilization Bar.SLDPRT, Steering Column Assembly.SLDASM]
2018-04-17 submit button on welcome page now working
2018-04-17 Added no cap versions of solidworks files
    [Axel Rotator.SLDPRT, Driver Bar No Caps.SLDPRT, Stabilization Bar No Caps.SLDPRT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]
2018-04-19 timer stuff
2018-04-19 Fixed Timer
2018-04-19 socket emit on QUIT button
2018-04-19 Resized Parts
    [Axel Rotator.SLDPRT, Steering Column Assembly.SLDASM, Steering Column Base New.SLDPRT]
2018-04-19 socket emit on new game
2018-04-19 Added a logout button
2018-04-29 Updated
    1. Added an image to the login page, which is technically the play game button
    2.I attached the image
    3. the Final game stats & analytics take backend data now
2018-04-29 Updated
    Changed some styles
    Created a timer on Final game stats so it would return back to the main page.
2018-04-29 wiring diagram and new .jar
    [Arena.fzz]
